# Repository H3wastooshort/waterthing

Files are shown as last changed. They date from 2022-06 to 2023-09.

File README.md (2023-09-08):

# waterthing
Wierd Garden Watering system

# very bad build guide
contact me if anything goes wrong (it will)
i will try to help if you actually want to build this
## controller
1. 3d print the case parts for the controller or come up with your own
2. put the parts in position and hotglue and screw them down
3. connect the components according to the schematic. the schematic is not the definitive way to do it though but rather a reflection of the current state of my build.
   the LoRa and LED module are optional.
4. upload the sketch and check if everything powers up and works
5. go mad because you cant find *that one error*
## gateway
1. (optional) print case and attach ESP32 LoRa Board 
2. connect antenna
3. upload sketch
4. connect to config AP and input WiFi credentials

# all shit blow this is outdated, just ignore it i will fix it some day....

## pump concept
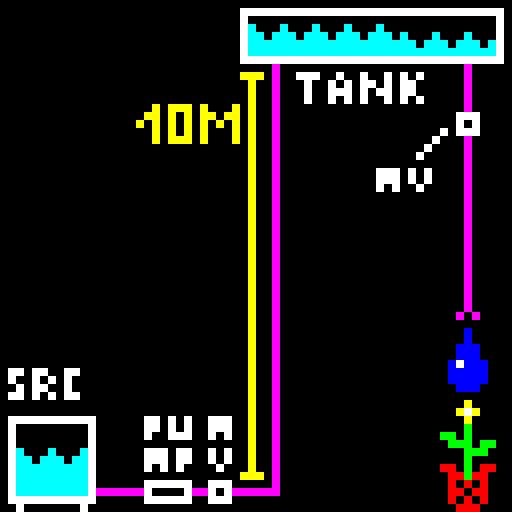
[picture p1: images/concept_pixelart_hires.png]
concept pixelart of the setup

 
The irrigation system is supposed to irrrigate via leaky hoses wich can only output little flow.

Most normal pumps can't efficiently provide this constant pressure, low flowrate flow, wich is bad becuase im planning to power this off of solar.

To fix this, the pump fills a tank about 10 meters higher, then shuts off and waits for the tank to drain out the leaky hoses after opening a magnet valve. Anadditional magnet valve is directly after the pump to prevent backflow.

This cycle is repeated until the desired amout of irrigation took place (or the water source is empty).

## tank concept
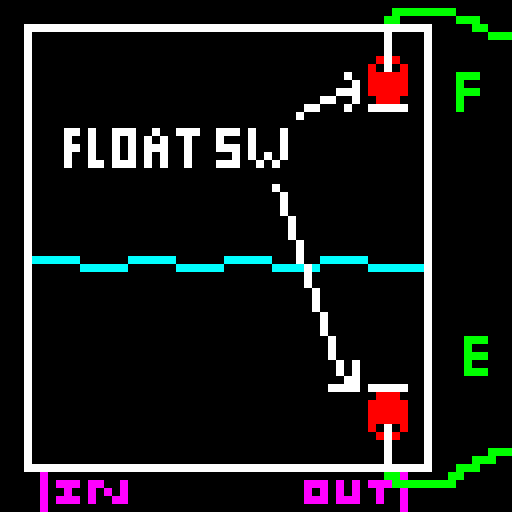
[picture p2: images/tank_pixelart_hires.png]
concept pixelart of the tank


The tank has a full and empty float switch. Both pull the arduino pin low when underwater

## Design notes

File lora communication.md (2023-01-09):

# General Scheme
[Magic Number][Packet ID][Packet Type][Data]

Magic Number is just 42

Packet ID increment individually on each side and rolls over to 0 when going over 255

## Gateway -> Water System
| Packet Type | Name | Anatomy | Description / Comment |
| --- | ---- | --- | --- |
| 0 | Current Time | [1 byte Packet ID of 230 time req] [UNIX Timestamp 32bit] | yes Y2K38, i'll just add the 60-something years when it rolls over to 1970 |
| 1 | Add Water to Irrigate | [1 byte Packet ID of challange] [Liters 2 bytes] [Auth Response 32 bytes] | |
| 2 | Cancel Irrigation | [1 byte Packet ID of challange] [Auth Response 32 bytes] | |
| 3 | Set Irrigation Timer | [1 byte Packet ID of challange] [Hour 1 byte] [Minute 1 byte] [Liters 2 bytes] [Auth Response 32 bytes] | |
| 241 | Reboot Notification | No Data | Packet sent once on boot |
| 250 | Ask for Auth challange | No Data | |
| 251 | Ping | | |
| 252 | Check Auth | [1 byte Packet ID of challange] [Auth Response 32 bytes] | Debug command to see if you have the right key without doing sth |
| 255 | ACK | [Packet ID] | |

## Water System -> Gateway
| Packet Type | Name | Anatomy | Description / Comment |
| --- | ---- | --- | --- |
| 0 | System Status | [4+4 bit status] [2 byte fixed point battery voltage]| Used to broadcast system state like STATUS_IDLE. Left 4 bits are system state, right 4 ones are more info (for ex in idle: alread watered, turned off, etc). fixed point battery voltage is a uint16_t divided by 100. max value would be 65.535V |
| 1 | Watering State | [4+4 bit status] [2 byte unsigned int: liters left] [2 byte unsigned int: liters called] | broadcasts watering state if currently watering |
| 230 | Request Time | No Data | |
| 240 | Reboot Notification | No Data | Packet sent once on boot |
| 249 | ACK | [1 byte packet ID] | |
| 250 | Auth challange | [1 byte Packet ID of 250 ask] [Auth challange 16 bytes] | |
| 251 | No Challange | [1 byte Packet ID] | Ask for a Challange Fist |
| 253 | Commands disabled | [1 byte Packet ID] | |
| 254 | Command Not Authenticated | [1 byte Packet ID] | |
| 255 | Command OK | [1 byte Packet ID] |

## Ground Sensor -> Water System
**JUST AN IDEA. PROBABLY WON'T HAPPEN**
| Packet Type | Name | Anatomy | Description / Comment |
| --- | ---- | --- | --- |
| 100 | Ground Data | [Sensor ID 1 byte] [Wetness 1 byte] | ground wetness is 0%-100% in 0.5% steps (so 0-200 in the wetness byte) |

## broadcast
 * Broadcast packets are removed from queue after they get acknowledged by the gateway or after 5 retransmits (spaced 5 seconds apart)
 * 

## system status
0bLLLLRRRR
### Left
| Bits | State |
| ---- | ----- |
| 0000 | Idle |
| 0001 | Pumping |
| 0010 | Emptying |
| 0011 | Afterdrain |
| 0100 | NO WATER |
| 0101 | LOW BATTERY |
| 0110 | NO TIME |
| 0111 | GENERAL FAIL |
### Right
#### Idle
| Bits | Extra |
| ---- | ----- |
| 0000 | Normal |
| 0001 | Off |
| 0010 | Done Today |
| 0011 | Rain |
#### General Fail
[] = 1 bit, each can be set individually

[Tank Sensors][RTC Missing][RTC Unset][Unused]

## (probably insecure) Authentication
 0. User saves 16 byte password from Water Systems Serial Console into the Gateway and requests an action.
 1. Gateway attempts up to 5 times to request an auth challange
 2. Water System respondes with a 16 byte random value as a challange.
 3. Gateway appends puts challange pass and packet data into sha-256 ([chal][pass][packet type][data] -> sha256)
 4. Gateway transmits the command id and parameters followed by the 32 bytes of the sha-256 hash
 5. arduino performs the same sha256 on challange value + security key and checks if they are identical
 6. command is accepted or rejected depending on hashes matching or not

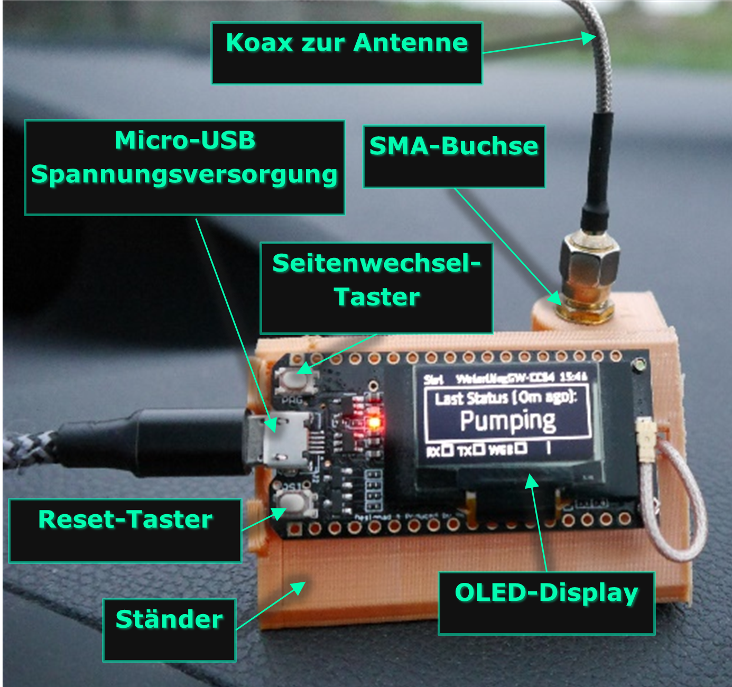
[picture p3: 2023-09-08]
images/gw overview.png

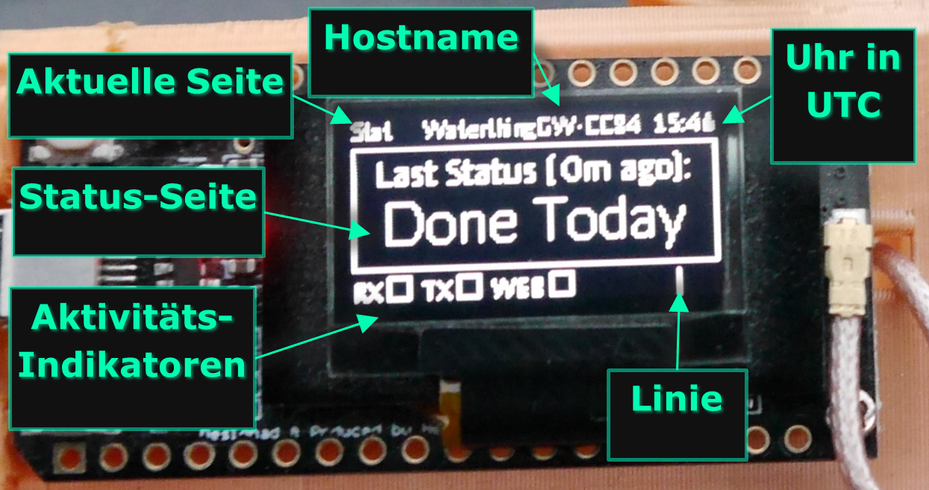
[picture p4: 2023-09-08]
images/gw ui.png

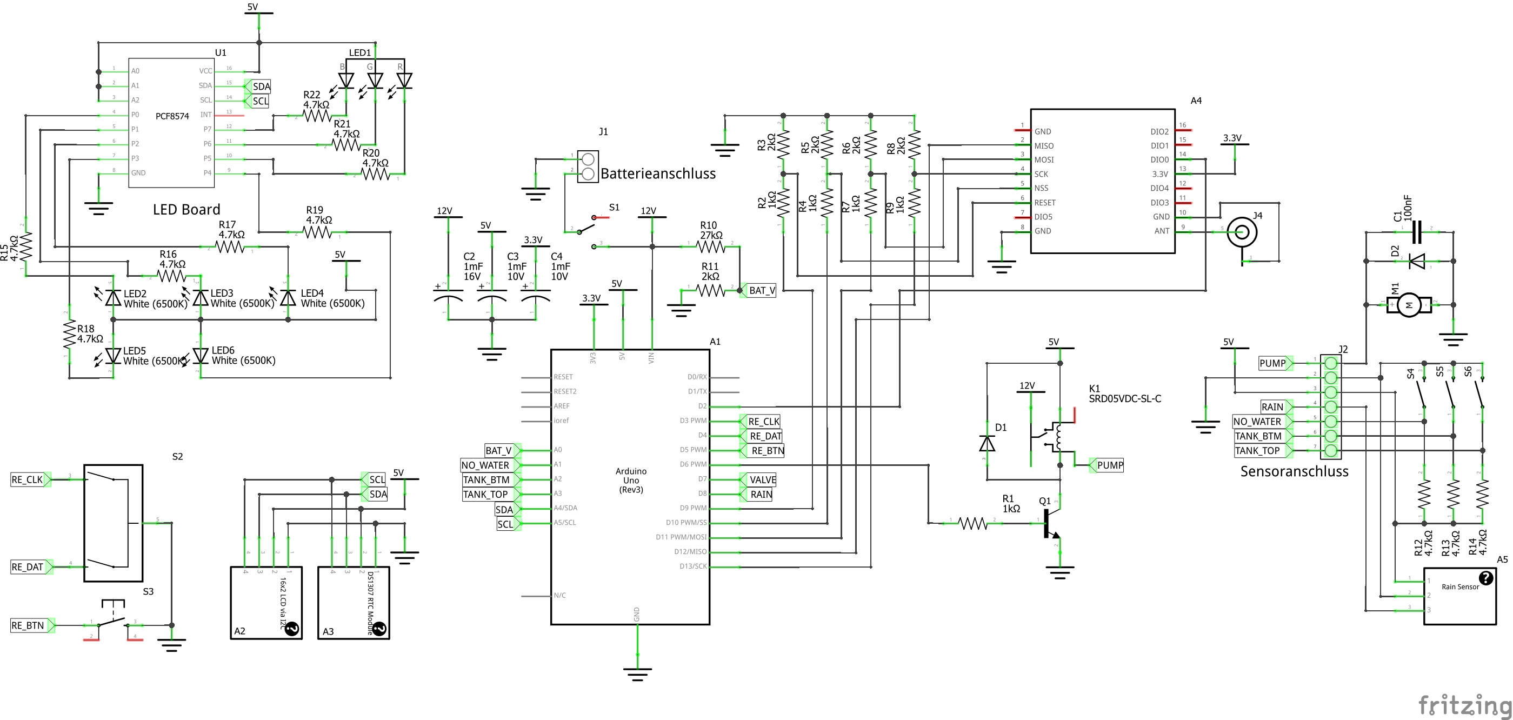
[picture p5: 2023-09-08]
images/wt circ_Schaltplan edit.png

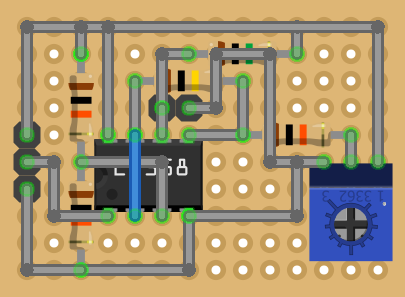
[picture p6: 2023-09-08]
images/opamp perfboarf_Steckplatine_sensitive.png

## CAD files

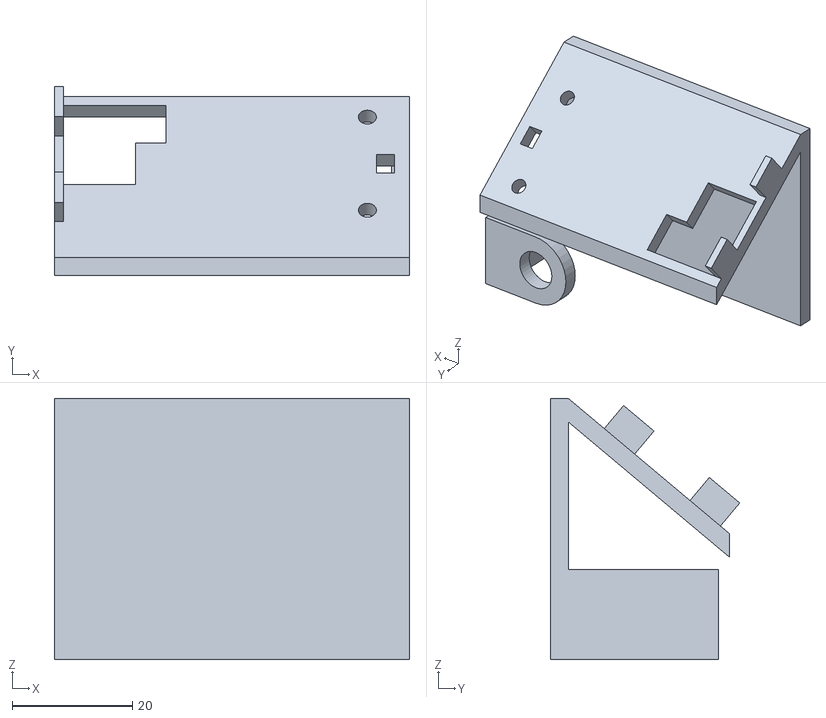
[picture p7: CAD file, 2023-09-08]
3d_models/GS Ständer.STL
59.0 x 31.5 x 43.4

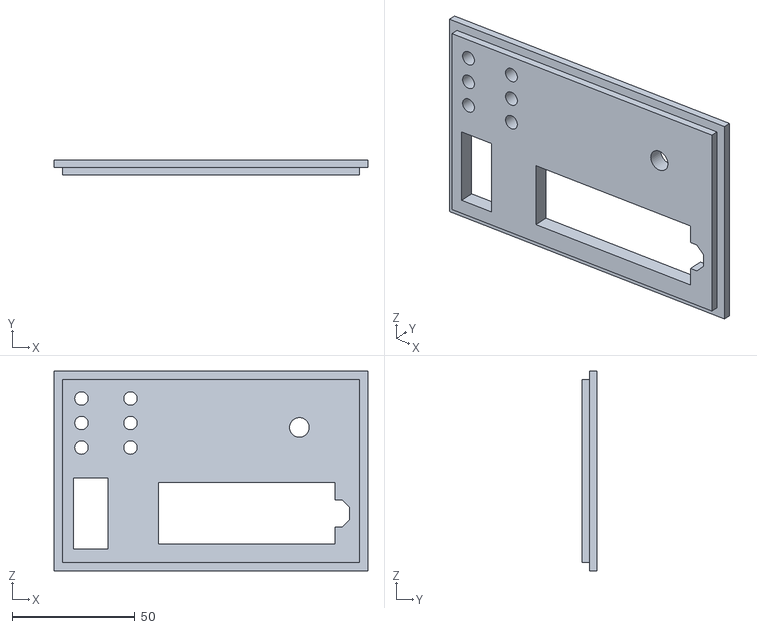
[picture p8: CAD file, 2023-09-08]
3d_models/deckel.STL
128.1 x 6.00 x 81.6

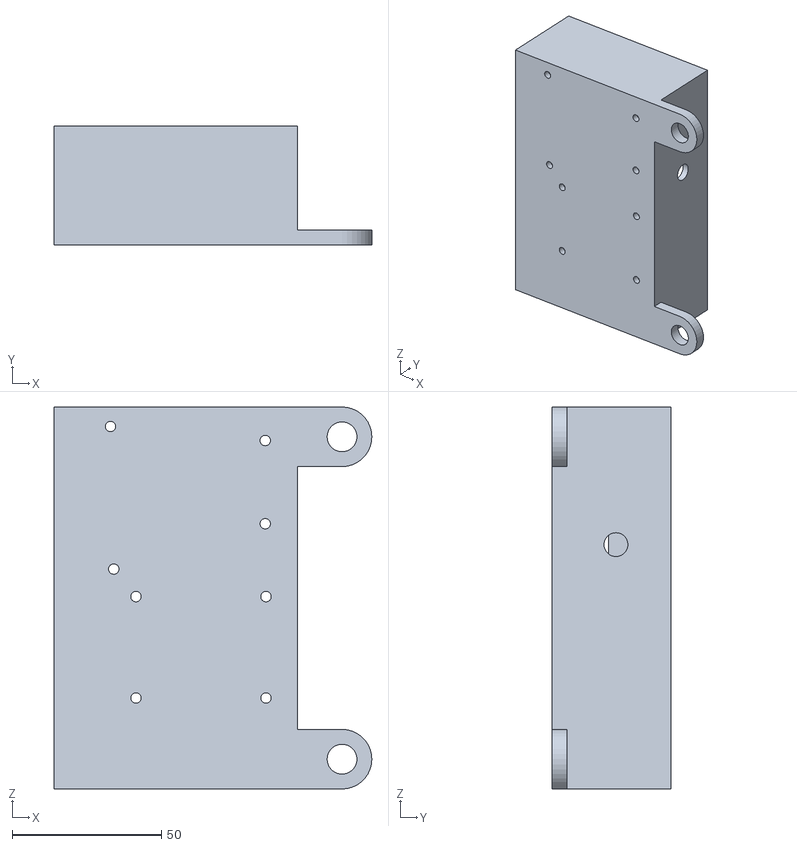
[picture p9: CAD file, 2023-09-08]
3d_models/gehäuse.STL
106.6 x 40.0 x 128.1

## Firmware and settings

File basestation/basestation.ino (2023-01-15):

//Gateway

#include <EEPROM.h>
#include <LoRa.h>
#include <Wire.h>
#include "fonts.h"
#include <OLEDDisplay.h>
#include <SSD1306Wire.h>  //https://github.com/ThingPulse/esp8266-oled-ssd1306
#include <WiFi.h>
#include <WiFiManager.h>  //https://github.com/tzapu/WiFiManager
#include <NTPClient.h>    //https://github.com/arduino-libraries/NTPClient
#include <RTClib.h>       //https://github.com/adafruit/RTClib/
#include <WebServer.h>
#include <EMailSender.h>  //https://github.com/xreef/EMailSender
#include <SPIFFS.h>
#define ARDUINOJSON_USE_LONG_LONG 1
#include <ArduinoJson.h>
#include <ESPmDNS.h>
#include <ArduinoOTA.h>
#include <map>
#include "mbedtls/md.h"

#undef LED_BUILTIN
#define LED_BUILTIN 25

#define RED_LED_PIN 12
#define GREEN_LED_PIN 13
#define BLUE_LED_PIN 21

#define LORA_FREQ 869525000        //869.525mhz is allowed to be used at 100mW 10% duty cycle (360 sec an hour) in germany (NO WARRANTY ON THAT!)
#define LORA_TX_PWR 20             // 20dbm/100mW is max
#define LORA_RETRANSMIT_TIME 5000  //time between retransmit attempts in ms
#define LORA_RETRANSMIT_TRIES 5
#define LORA_MAGIC 42
#define LORA_TX_INTERVAL 300000  //time between beacon broadcasts in ms
#define LORA_MAX_AIRTIME 340     //in seconds

#define LORA_CS_PIN 18
#define LORA_RST_PIN 14
#define LORA_DIO0_PIN 26

#define OLED_FPS 30
#define OLED_ADDRESS 0x3c
#define OLED_SDA_PIN 4
#define OLED_SCL_PIN 15
#define OLED_RST_PIN 16

#define EEPROM_SIZE 512

#define RTC_SDA_PIN 21
#define RTC_SCL_PIN 13

char host_name[18] = "WaterthingGW-XXXX";  // last 4 chars will be chip-id

SSD1306Wire oled(OLED_ADDRESS, -1, -1, GEOMETRY_128_64 /*, I2C_ONE, 200000*/);  //sometimes I2C_ONE is not decalred, sometimes it is, idk why
WiFiManager wm;
WiFiUDP ntpUDP;
NTPClient ntp(ntpUDP, "europe.pool.ntp.org", 0, 60000);
RTC_DS1307 rtc;
WebServer server(80);
EMailSender email("", "", "", "", 0);

//conf
struct settings_s {
  char conf_ssid[16] = "WaterthingGW";
  char conf_pass[16] = "CHANGE_ME_42";
  uint8_t lora_security_key[16] = { 0 };
  char alert_email[32] = "max.mustermann@example.com";
  char smtp_server[32] = { 0 };
  char smtp_user[32] = { 0 };
  char smtp_pass[32] = { 0 };
  uint16_t smtp_port = 465;  //usually 465 for SSL SMTP
  char web_user[32] = "waterthing";
  char web_pass[32] = "thisisnotsecure";
  uint8_t display_brightness = 255;
  char ntp_server[32] = "europe.pool.ntp.org";
  uint32_t crc;  //TODO: implement this
} settings;

//time
uint64_t current_timestamp;
bool rtc_ok = false;
uint8_t current_hour = 0;
uint8_t current_min = 0;

//lora
uint8_t lora_outgoing_packet_id = 1;      //increments every packet
byte lora_outgoing_queue[4][48] = { 0 };  //holds up to 4 messages that are to be sent with max 48 bits. first byte is magic, 2nd message id, 3nd is message type, rest is data. if all 0, no message in slot. set to 0 after up to 0 retransmits
uint8_t lora_outgoing_queue_idx = 0;      //idx where to write
uint64_t lora_outgoing_queue_last_tx = 0;
uint8_t lora_outgoing_queue_tx_attempts[4] = { 0 };
bool lora_tx_ready = true;
uint64_t lora_tx_start_millis = 0;
uint64_t lora_airtime = 0;  //in millis

byte lora_incoming_queue[4][48] = { 0 };      //holds up to 4 messages that are to be sent with max 48 bits.
uint8_t lora_incoming_queue_idx = 0;          //idx where to write
uint16_t lora_incoming_queue_len[4] = { 0 };  //lengths of recieved packages
byte lora_last_incoming_message_IDs[16] = { 0 };
uint8_t lora_last_incoming_message_IDs_idx = 0;

//shared stuff start
enum lora_packet_types_ws_to_gw {  //water system to gateway
  PACKET_TYPE_STATUS = 0,
  PACKET_TYPE_WATER = 1,
  PACKET_TYPE_TEST = 69,
  PACKET_TYPE_REBOOT = 240,
  PACKET_TYPE_WS_ACK = 249,
  PACKET_TYPE_AUTH_CHALLANGE = 250,
  PACKET_TYPE_NO_CHALLANGE = 251,
  PACKET_TYPE_CMD_DISABLED = 253,
  PACKET_TYPE_CMD_AUTH_FAIL = 254,
  PACKET_TYPE_CMD_OK = 255,
};

enum lora_packet_types_gw_to_ws {  //gateway to water system
  PACKET_TYPE_CURRENT_TIME = 0,
  PACKET_TYPE_ADD_WATER = 1,
  PACKET_TYPE_CANCEL_WATER = 2,
  PACKET_TYPE_SET_TIMER = 3,
  PACKET_TYPE_GW_REBOOT = 241,
  PACKET_TYPE_REQUST_CHALLANGE = 250,
  PACKET_TYPE_ACK = 255
};

//length is only packet data. add 3 for real packet size
uint8_t ws_to_gw_packet_type_to_length(uint8_t pt) {
  switch (pt) {
    case PACKET_TYPE_STATUS: return 3; break;
    case PACKET_TYPE_WATER: return 5; break;
    case PACKET_TYPE_TEST: return 5; break;
    case PACKET_TYPE_AUTH_CHALLANGE: return 17; break;
    case PACKET_TYPE_CMD_DISABLED: return 0; break;
    case PACKET_TYPE_CMD_AUTH_FAIL: return 1; break;
    case PACKET_TYPE_CMD_OK: return 1; break;
    case PACKET_TYPE_REBOOT: return 0; break;
    case PACKET_TYPE_WS_ACK: return 1; break;
    default: return 47; break;
  }
}

uint8_t gw_to_ws_packet_type_to_length(uint8_t pt) {
  switch (pt) {
    case PACKET_TYPE_ACK: return 1; break;
    case PACKET_TYPE_REQUST_CHALLANGE: return 0; break;
    case PACKET_TYPE_CURRENT_TIME: return 0; break;
    case PACKET_TYPE_ADD_WATER: return 35; break;
    case PACKET_TYPE_CANCEL_WATER: return 33; break;
    case PACKET_TYPE_SET_TIMER: return 37; break;
    case PACKET_TYPE_GW_REBOOT: return 0; break;
  }
}
//shared stuff end

//recieved stuff
int16_t last_lora_rssi = 0xFFFF;
int16_t last_lora_snr = 0xFFFF;
int32_t last_lora_freq_error = 0xFFFFFFFF;
uint64_t last_recieved_packet_time = 0;  //time in unix timestamp

byte last_wt_status = 0xFF;  //left bytes main status, right 4 bytes extra status
uint64_t last_wt_status_timestamp = 0;
uint16_t last_liters_left = 0xFFFF;    //0xFFFF means not known, 0x0000 means done
uint16_t last_liters_called = 0xFFFF;  //0xFFFF means not known, 0x0000 means done
uint64_t last_wt_liters_timestamp = 0;
float last_wt_battery_voltage = -1;
uint64_t last_wt_battery_voltage_timestamp = 0;
uint64_t last_wt_reboot_timestamp = 0;

//authed lora cmds
enum auth_state_e {
  AUTH_STEP_IDLE = 0,  //wait for entry in lora_auth_cmd_queue
  AUTH_STEP_TX_CHALLANGE_REQUEST = 1,
  AUTH_STEP_WAIT_CHALLANGE = 2,
  AUTH_STEP_TX_ANSWER = 3,
  AUTH_STEP_WAIT_CMD_SUCCESS = 4,
} auth_state;
byte last_wt_challange[16] = { 0 };       //if all 0, not valid/non recieved
byte lora_auth_cmd_queue[4][16] = { 0 };  //the data part of all authed commands to be sent.
uint8_t lora_auth_cmd_queue_idx = 0;
uint8_t lora_auth_packet_processing = 255;  //255 means invalid
byte last_auth_cmd_response = 0;            //0 means invalid
byte last_auth_challange_packet_id = 0xFF;
uint64_t last_auth_packet_millis = 0;

//web
char web_login_cookies[256][32];
uint8_t web_login_cookies_idx = 0;

std::map<byte, String> status_to_text{
  // SSSSEEEE
  { 0b11111111, "Unknown" },
  { 0b00000000, "Idle" },
  { 0b00000001, "Off" },
  { 0b00000010, "Done Today" },
  { 0b00000011, "Too Rainy" },
  { 0b00010000, "Pumping" },
  { 0b00100000, "Emptying" },
  { 0b00110000, "Afterdrain" },
  { 0b01000000, "NO WATER" },
  { 0b01010000, "LOW BAT." },
  { 0b01100000, "NO TIME" },
  { 0b01110000, "GEN. FAIL" },
  { 0b01110001, "PUMP FAIL" },
  { 0b01111000, "TS FAIL" },
  { 0b01110110, "RTC FAIL" },
  { 0b01110100, "RTC FAIL" },
  { 0b01110010, "RTC UNSET" },
  { 0b01111100, "TS+RTC FAIL" },
  { 0b01111110, "TS+RTC FAIL" },
  { 0b01111010, "TS+RTC FAIL" },
  { 0b01111101, "TOTAL FAIL" },
  { 0b01111111, "TOTAL FAIL" },
  { 0b01111011, "TOTAL FAIL" }
};

//display
enum gw_page_e { PAGE_STATUS = 0,
                 PAGE_WT = 1,
                 PAGE_LORA = 2,
                 PAGE_WIFI = 3 };
uint8_t disp_page = 0;
std::map<uint8_t, String> gw_page_to_text{
  { PAGE_STATUS, "Stat" },
  { PAGE_WT, "WT" },
  { PAGE_LORA, "LoRa" },
  { PAGE_WIFI, "WiFi" }
};
uint8_t rx_indicator_blink = 0;
//uint8_t tx_indicator_blink = 0;
uint8_t web_indicator_blink = 0;
uint8_t tx_indicator_pos = 0;

uint64_t last_disp_button_down = 0;
void IRAM_ATTR disp_button_down() {
  if (millis() - last_disp_button_down > 250) disp_page++;
  if (disp_page > 3) disp_page = 0;
  last_disp_button_down = millis();
}

//stuff
void update_time() {
  ntp.update();
  if (rtc_ok and rtc.isrunning() and !ntp.isTimeSet()) {  //if RTC is OK but the NTP server is not
    DateTime tnow = rtc.now();
    current_timestamp = tnow.unixtime();
    current_min = tnow.minute();
    current_hour = tnow.hour();
  } else {  //ELSE if ntp ok OR if rtc and ntp bad (ntp client will still calculate time with millis)
    current_timestamp = ntp.getEpochTime();
    current_min = ntp.getMinutes();
    current_hour = ntp.getHours();
  }
}

char randomASCII() {  //give random lowercase ascii
  switch (random(0, 3)) {
    default:
    case 0:
      return max(min(uint8_t(random(0, 24) + 'a'), uint8_t('z')), uint8_t('a'));
      break;

    case 1:
      return max(min(uint8_t(random(0, 24) + 'A'), uint8_t('Z')), uint8_t('A'));
      break;

    case 2:
      return max(min(uint8_t(random(0, 10) + '0'), uint8_t('9')), uint8_t('0'));
      break;
  }
}

void handle_lora_packet(int packet_size) {                                                 //TODO: maybe move magic checking here
  if (packet_size <= 48) {                                                                 //3840 is an erronious recieve
    for (uint8_t b = 0; b < 48; b++) lora_incoming_queue[lora_incoming_queue_idx][b] = 0;  //firstly clear

    for (uint8_t b = 0; (b < min(packet_size, 48)) and LoRa.available(); b++) {
      lora_incoming_queue[lora_incoming_queue_idx][b] = LoRa.read();
    }

    last_lora_rssi = LoRa.packetRssi();
    last_lora_snr = LoRa.packetSnr();
    last_lora_freq_error = LoRa.packetFrequencyError();
    lora_incoming_queue_len[lora_incoming_queue_idx] = min(packet_size, 48);
    lora_incoming_queue_idx++;
    if (lora_incoming_queue_idx >= 4) lora_incoming_queue_idx = 0;
  }
  LoRa.flush();  //clear packet if for some reason the is anything left
}

void handle_lora_tx_done() {
  LoRa.receive();
  lora_airtime += millis() - lora_tx_start_millis;  //add tx time
  lora_tx_ready = true;
}

//display
uint8_t alive_line_pos = 125;
bool alive_line_dir = false;  //false towards left, true towards right
void draw_display_boilerplate() {
  oled.clear();
  oled.setColor(WHITE);
  oled.setFont(Lato_Thin_8);
  oled.drawRect(0, 11, 127, 42);  //content outline

  //page number
  oled.setTextAlignment(TEXT_ALIGN_LEFT);
  oled.drawString(0, 0, gw_page_to_text[disp_page]);

  //name
  oled.setTextAlignment(TEXT_ALIGN_CENTER);
  oled.drawString(63, 0, host_name);

  //time on the right
  oled.setTextAlignment(TEXT_ALIGN_RIGHT);
  char time_buf[5];
  sprintf(time_buf, "%02d:%02d", current_hour, current_min);
  oled.drawString(127, 0, (String)time_buf);

  //rx/tx indicators
  oled.setTextAlignment(TEXT_ALIGN_LEFT);
  uint8_t bottom_pos = 0;
  oled.drawString(bottom_pos, 55, "RX");
  bottom_pos += oled.getStringWidth("RX") + 2;
  if (rx_indicator_blink > 0) {
    oled.fillRect(bottom_pos, 55, 8, 8);
    rx_indicator_blink--;
  } else oled.drawRect(bottom_pos, 55, 8, 8);
  bottom_pos += 8 + 4;
  oled.drawString(bottom_pos, 55, "TX");
  bottom_pos += oled.getStringWidth("TX") + 2;
  tx_indicator_pos = bottom_pos;
  //if (tx_indicator_blink > 0) {
  if (!lora_tx_ready) {
    oled.fillRect(bottom_pos, 55, 8, 8);
    //tx_indicator_blink--;
  } else oled.drawRect(bottom_pos, 55, 8, 8);
  bottom_pos += 8 + 4;
  oled.drawString(bottom_pos, 55, "WEB");
  bottom_pos += oled.getStringWidth("WEB") + 2;
  if (web_indicator_blink > 0) {
    oled.fillRect(bottom_pos, 55, 8, 8);
    web_indicator_blink--;
  } else oled.drawRect(bottom_pos, 55, 8, 8);
  bottom_pos += 8 + 4;

  //moving line to show its alive
  alive_line_pos += alive_line_dir ? 1 : -1;
  if (alive_line_pos >= 125) alive_line_dir = false;
  if (alive_line_pos <= bottom_pos) alive_line_dir = true;
  oled.drawLine(alive_line_pos, 55, alive_line_pos, 63);
}

void config_ap_callback(WiFiManager *myWiFiManager) {
  //put conf AP credentials on screen
  oled.clear();
  oled.setColor(WHITE);
  oled.setFont(Lato_Thin_8);
  oled.setTextAlignment(TEXT_ALIGN_LEFT);

  oled.drawString(0, 0, "Connect AP and visit");
  oled.drawString(0, 10, "http://192.168.4.1/");
  oled.drawString(0, 20, "SSID:");
  oled.drawString(0, 30, settings.conf_ssid);
  oled.drawString(0, 40, "Password:");
  oled.drawString(0, 50, settings.conf_pass);
  oled.display();
}

//web
void set_mail_conf() {
  email.setSMTPServer(settings.smtp_server);
  email.setNameFrom(host_name);
  email.setEMailFrom(settings.smtp_user);
  email.setEMailLogin(settings.smtp_user);
  email.setEMailPassword(settings.smtp_pass);
  email.setSMTPPort(settings.smtp_port);
  email.setIsSecure(false);

  email.setEHLOCommand(true);
  //email.setAdditionalResponseLineOnHELO(2);  //only use on versions without auto-add.resp.l.. works for german mailer GMX. you probably have to figure out your value by setting it higher, uncommenting EMAIL_SENDER_DEBUG in EMailSenderKey.h and reducing it when error says so
}

bool check_auth() {
  Serial.println(F("Authed Access Attempt"));
  bool authed = false;

  if (server.hasHeader("Cookie")) {
    String cookie_header = server.header("Cookie");
    uint16_t lc_start = cookie_header.indexOf("login_cookie=");
    uint16_t lc_end = cookie_header.substring(lc_start).indexOf("; ");
    if (lc_end == 0) lc_end = cookie_header.length() - lc_start;
    const char *login_cookie = cookie_header.substring(lc_start + 13, lc_end).c_str();

    //Serial.print(F(" * Header: "));
    //Serial.println(cookie_header);
    //Serial.print(F(" * Cookie: "));
    //Serial.println(login_cookie);
    //Serial.print(F(" * Cookie Length: "));
    //Serial.println(login_cookie.length());

    if (strlen(login_cookie) == 31) {
      for (uint16_t c = 0; c < 256; c++) {  //check if login cookie valid
        //Serial.print(F(" * Cookie Candidate: "));
        //Serial.println(correct_l_cookie);

        if (strcmp(login_cookie, (const char *)web_login_cookies[c]) == 0) {
          authed = true;
          break;
        }
      }
    }
  } else Serial.println(F(" * Cookie Header Missing"));

  Serial.print(F(" * "));
  Serial.println(authed ? F("SUCCESS") : F("FAIL"));
  Serial.println();
  return authed;
}

void rest_status() {
  web_indicator_blink += 1;
  DynamicJsonDocument stuff(1024);
  stuff["status"]["state"] = last_wt_status >> 4;
  stuff["status"]["extra"] = last_wt_status & 0b00001111;
  stuff["status"]["as_text"] = status_to_text[last_wt_status];
  stuff["status"]["timestamp"] = last_wt_status_timestamp;
  stuff["irrigation"]["left"] = last_liters_left;
  stuff["irrigation"]["called"] = last_liters_called;
  stuff["irrigation"]["timestamp"] = last_wt_liters_timestamp;
  stuff["battery"]["voltage"] = last_wt_battery_voltage;
  stuff["battery"]["timestamp"] = last_wt_battery_voltage_timestamp;
  stuff["other"]["last_reboot"] = last_wt_reboot_timestamp;
  stuff["lora_rx"]["last_rssi"] = last_lora_rssi;
  stuff["lora_rx"]["last_snr"] = last_lora_snr;
  stuff["lora_rx"]["last_freq_error"] = last_lora_freq_error;
  stuff["lora_rx"]["last_packet_time"] = last_recieved_packet_time;
  stuff["lora_tx"]["airtime"] = (double)lora_airtime / 1000;
  stuff["lora_tx"]["max_airtime"] = LORA_MAX_AIRTIME;
  stuff["gateway"]["wifi"]["ssid"] = WiFi.SSID();
  stuff["gateway"]["wifi"]["rssi"] = WiFi.RSSI();
  stuff["gateway"]["time"]["now"] = current_timestamp;
  stuff["gateway"]["time"]["rtc_ok"] = rtc_ok;
  stuff["gateway"]["time"]["ntp_ok"] = ntp.isTimeSet();
  char json_stuff[2048];
  serializeJsonPretty(stuff, json_stuff);
  server.sendHeader("Refresh", "10");
  server.send(200, "application/json", json_stuff);
}

void rest_login_get() {
  DynamicJsonDocument resp(128);
  server.send(200, "application/json", check_auth() ? "true" : "false");
}

void rest_login() {
  web_indicator_blink += 1;
  if (check_auth()) {
    server.send(200, "application/json", "{\"success\":\"Already Authenticated.\"}");
    Serial.println(F("Login Attempt: Already Authed"));
    return;
  }

  Serial.println(F("Login Attempt"));

  DynamicJsonDocument login(128);
  if (server.hasArg("plain")) deserializeJson(login, server.arg("plain"));
  String user = server.hasArg("plain") ? login["user"] : server.arg("user").c_str();
  String pass = server.hasArg("plain") ? login["pass"] : server.arg("pass").c_str();
  String correct_user = settings.web_user;
  String correct_pass = settings.web_pass;

  Serial.print(F(" * User: "));
  Serial.println(user);
  Serial.print(F(" * Pass: "));
  Serial.println(pass);
  Serial.print(F(" * Correct User: "));
  Serial.println(correct_user);
  Serial.print(F(" * Correct Pass: "));
  Serial.println(correct_pass);

  if (user.equals(correct_user) and pass.equals(correct_pass)) {
    for (uint8_t b = 0; b < 31; b++) web_login_cookies[web_login_cookies_idx][b] = randomASCII();
    web_login_cookies[web_login_cookies_idx][31] = 0;
    String cookiestring = "login_cookie=";
    cookiestring += web_login_cookies[web_login_cookies_idx];
    cookiestring += "; Path=/admin/; SameSite=Strict; Max-Age=86400";  //cookie kept for a day

    server.sendHeader("Set-Cookie", cookiestring);
    if (!server.hasArg("plain")) server.sendHeader("Refresh", "3;url=/admin/control.html");
    server.send(200, "application/json", "{\"success\":\"Authenticated\",\"login_cookie\":\"" + cookiestring + "\"}");
    Serial.println(F(" * SUCCESS"));
  } else {
    if (!server.hasArg("plain")) server.sendHeader("Refresh", "5;url=/admin/login.html");
    server.send(403, "application/json", "{\"error\":\"Credentials invalid.\"}");
    Serial.println(F(" * FAIL"));
  }

  Serial.println();
}

void rest_control() {
  web_indicator_blink += 1;
  if (!check_auth()) {
    server.send(403, "application/json", "{\"error\":403}");
    return;
  }
  uint16_t status_code = 200;
  DynamicJsonDocument resp(512);

  DynamicJsonDocument req(256);
  if (server.hasArg("plain")) deserializeJson(req, server.arg("plain"));

  if (req["call_for_water"].is<uint16_t>() or server.hasArg("call_for_water")) {
    for (uint8_t b = 0; b < 16; b++) lora_auth_cmd_queue[lora_auth_cmd_queue_idx][b] = 0;
    union {
      uint16_t water_call = 0;
      byte water_call_b[2];
    };
    water_call = server.hasArg("plain") ? req["call_for_water"] : server.arg("call_for_water").toInt();

    lora_auth_cmd_queue[lora_auth_cmd_queue_idx][0] = PACKET_TYPE_ADD_WATER;
    lora_auth_cmd_queue[lora_auth_cmd_queue_idx][1] = water_call_b[0];
    lora_auth_cmd_queue[lora_auth_cmd_queue_idx][2] = water_call_b[1];

    lora_auth_cmd_queue_idx++;
    if (lora_auth_cmd_queue_idx >= 4) lora_auth_cmd_queue_idx = 0;

    resp["success"] = "queued <water call> command";
  }

  else if (req["cancel_water"] or server.hasArg("cancel_water")) {
    for (uint8_t b = 0; b < 16; b++) lora_auth_cmd_queue[lora_auth_cmd_queue_idx][b] = 0;

    lora_auth_cmd_queue[lora_auth_cmd_queue_idx][0] = PACKET_TYPE_CANCEL_WATER;

    lora_auth_cmd_queue_idx++;
    if (lora_auth_cmd_queue_idx >= 4) lora_auth_cmd_queue_idx = 0;

    resp["success"] = "queued <cancel> command";
  }

  else if (req["set_timer"] or server.hasArg("set_timer")) {
    for (uint8_t b = 0; b < 16; b++) lora_auth_cmd_queue[lora_auth_cmd_queue_idx][b] = 0;
    union {
      uint16_t liters = 0;
      byte liters_b[2];
    };
    liters = server.hasArg("plain") ? req["set_timer"]["liters"] : server.arg("set_timer_liters").toInt();

    lora_auth_cmd_queue[lora_auth_cmd_queue_idx][0] = PACKET_TYPE_SET_TIMER;
    lora_auth_cmd_queue[lora_auth_cmd_queue_idx][1] = server.hasArg("plain") ? req["set_timer"]["hour"] : server.arg("set_timer_hour").toInt();
    lora_auth_cmd_queue[lora_auth_cmd_queue_idx][2] = server.hasArg("plain") ? req["set_timer"]["minute"] : server.arg("set_timer_minute").toInt();
    lora_auth_cmd_queue[lora_auth_cmd_queue_idx][3] = liters_b[0];
    lora_auth_cmd_queue[lora_auth_cmd_queue_idx][4] = liters_b[1];

    lora_auth_cmd_queue_idx++;
    if (lora_auth_cmd_queue_idx >= 4) lora_auth_cmd_queue_idx = 0;

    resp["success"] = "queued <set timer> command";
  }

  else {
    server.send(400, "application/json", "{\"error\":\"no command\"");
    return;
  }

  if (!server.hasArg("plain")) server.sendHeader("Refresh", "3;url=/admin/control.html");
  char buf[512];
  serializeJson(resp, buf);
  server.send(status_code, "application/json", buf);
}

void rest_control_status() {
  web_indicator_blink += 1;
  uint16_t status_code = 200;
  DynamicJsonDocument resp(128);

  uint8_t left_q = 0;
  for (uint8_t p = 0; p < 4; p++) {
    bool is_empty = true;
    for (uint8_t b = 0; b < 16; b++)
      if (lora_auth_cmd_queue[p][b] != 0) is_empty = false;
    if (!is_empty) left_q++;
  }

  resp["auth_state"] = auth_state;
  resp["left_in_queue"] = left_q;
  resp["last_auth_cmd_response"] = last_auth_cmd_response;
  resp["last_auth_packet_millis"] = last_auth_packet_millis;

  char buf[256];
  serializeJson(resp, buf);
  server.send(status_code, "application/json", buf);
}

void rest_admin_get() {
  web_indicator_blink += 1;
  if (!check_auth()) {
    server.send(403, "application/json", "{\"error\":403}");
    return;
  }
  uint16_t status_code = 200;
  DynamicJsonDocument resp(1024);
  //settings
  resp["wifi"]["conf_ssid"] = settings.conf_ssid;
  resp["wifi"]["conf_pass"] = settings.conf_pass;
  for (uint8_t b = 0; b < 16; b++) resp["lora"]["security_key"][b] = settings.lora_security_key[b];
  resp["mail"]["alert_email"] = settings.alert_email;
  resp["mail"]["smtp_server"] = settings.smtp_server;
  resp["mail"]["smtp_user"] = settings.smtp_user;
  //resp["mail"]["smtp_pass"] = settings.smtp_pass;
  resp["mail"]["smtp_port"] = settings.smtp_port;
  resp["web"]["user"] = settings.web_user;
  //resp["web"]["pass"] = settings.web_pass;

  char buf[2048];
  serializeJson(resp, buf);
  server.send(status_code, "application/json", buf);
}
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
void loop() {
  ArduinoOTA.handle();
  server.handleClient();
  update_time();

  update_display();
  handle_lora();

  delay(5);
}

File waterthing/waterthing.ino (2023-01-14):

//Bewässerungssystem

/*
  ====IMPORTANT====
  If you run into space issues (you will), install the Optiboot bootloader on your board (it saves about 1 kb space)
  and compile with the ATMega328P option in MiniCore (https://github.com/MCUdude/MiniCore)
  as that has the correct space limit and can turn on LTO (Link-time optimizations) to save even more space. good luck
*/

#include <EEPROM.h>
#include <LiquidCrystal_I2C.h>
#include "gfx.h"
#include <TimeLib.h>
#include <Wire.h>
#include <DS1307RTC.h>  //https://github.com/PaulStoffregen/DS1307RTC/
#include <math.h>
#include <pcf8574.h>  //https://github.com/MSZ98/pcf8574
#include <SPI.h>
#include <LoRa.h>  //https://github.com/sandeepmistry/arduino-LoRa
#include <avr/wdt.h>
#include "sha256_small.h"  //https://github.com/simonratner/Arduino-SHA-256

#define LOW_WATER_PIN A1
#define TANK_BOTTOM_PIN A2
#define TANK_TOP_PIN A3  //reused for water flow sensor when in direct mode. WARNING! change PCINT suff in setup() too!!
#define RAIN_DETECTOR_PIN 8
#define SENSOR_DEBOUNCE 1000
#define PUMP_PIN 6
#define VALVE_PIN 7
#define CONTROL_RELAY_INVERTED true

//pcf
#define LED_PCF_ADDR 0x3F
#define RED_LED_PIN 5
#define GREEN_LED_PIN 6
#define BLUE_LED_PIN 7
#define TB_SENSOR_LED 2  //tank bottom sensor indicator
#define TT_SENSOR_LED 1  //tank top sensor indicator
#define PUMP_LED 0
#define LORA_TX_LED 3
#define LORA_RX_LED 4

#define DEBOUNCE_DELAY 150
#define BTN_PIN 5          //PCINT
#define ENCODER_CLK_PIN 3  //WARNING! change PCINT suff in setup() too!!
#define ENCODER_DT_PIN 4
#define ENCODER_INVERT_DIRECTION false

#define LCD_BACKLIGHT_TIMEOUT 10000

#define BATTERY_VOLTAGE_PIN A0

#define EEPROM_MAGIC_NUMBER 42

#define LORA_FREQ 869525000        //869.525mhz is allowed to be used at 100mW 10% duty cycle (360 sec an hour) in germany
#define LORA_TX_PWR 20             //20dbm/100mW is max
#define LORA_RETRANSMIT_TIME 5000  //time between retransmit attempts in ms
#define LORA_RETRANSMIT_TRIES 5
#define LORA_MAGIC 42
#define LORA_TX_INTERVAL 1800000  //time between beacon broadcasts in ms (30min)
#define LORA_MAX_AIRTIME 340     //in seconds

//library stuff
LiquidCrystal_I2C lcd(0x27, 16, 2);
PCF8574 pcf(LED_PCF_ADDR);  //all addr pins to high

enum gfx_IDs {        //enum for naming display gfx ids
  GFX_ID_STATUS = 0,  //redefined dynamically
  GFX_ID_DYN_1 = 1,
  GFX_ID_DYN_2 = 2,
  GFX_ID_DYN_3 = 3,
  GFX_ID_UML_S = 4,
  GFX_ID_UML_A = 5,
  GFX_ID_UML_O = 6,
  GFX_ID_UML_U = 7,
  GFX_ID_ARROW_L = 126,
  GFX_ID_ARROW_R = 127
};

//structs are used to save to EEPROM more easily
struct settings_s {
  uint16_t tank_capacity = 10;                  //in L
  double battery_voltage_adc_divider = 68.267;  //1024 divided by this multiplier equals the battery voltage
  float battery_voltage_cutoff = 10.4;          //if this voltage is reached while the system is idle, a low battery waring is displayed. 0 means disable
  float battery_voltage_reset = 11.4;           //if this voltage is reached while the system is in low batters state, the system is set back to idle
  int16_t max_mins_per_refill = -1;             //error is thrown if the pump takes longer than that to fill the tank (5L/min pump wont take more than 5 minutes to fill a 20L tank)
  uint8_t afterdrain_time = 5;                  //keep draining for this amount of time after a cycle finishes to dry the tank out
  uint16_t clicks_per_liter = 1000;
  bool low_water_on_level = LOW;     //level of low water pin when the low water sensor detects low water. sensor will probably be mounted upside-down so no water means low
  bool tank_bottom_on_level = HIGH;  //level of TANK_BOTTOM_PIN when water has reached the bottom sensor. sensor will probably be mounted upside-down so on means high
  bool tank_top_on_level = LOW;      //level of TANK_TOP_PIN when water has reached the top sensor
  bool rain_detected_on_level = LOW;
  uint8_t rain_minutes_til_block = 5;    //if rain is detected for more than this time, it is officially raining
  uint16_t rain_minutes_til_clear = 60;  //if its not rainf or at least this time, watering will resume as normal
  bool block_water_after_rain = false;
  byte lora_security_key[16];
  uint8_t lora_enable = 0;   //0=off, 1=broadcast only, 2=control
  uint8_t pump_timeout = 0;  //in minutes. if filling the tank takes longer than this value, the system goes into a fail state
  //uint32_t crc; //maybe verify with a crc32 here
} settings;

struct i_timer_s {
  int8_t start_hour = 0;
  int8_t start_minute = 0;
  uint16_t fillings_to_irrigate = 0;  //how many tank fillings to irrigate. when 0, system is turned off.
  uint8_t last_watering_day = 0;
  uint16_t liters_to_pump = 0;  //when in direct mode (no tank) how much liters to pump out
} irrigation_timer;

//and also just to organize things
struct c_error_s {
  bool rtc_missing = false;
  bool rtc_unset = false;
  bool tank_sensors_irrational = false;
  bool lora_missing = false;
  bool pump_timed_out = false;
} component_errors;

//enums for easier code reading
enum system_state_e {
  STATUS_IDLE = 0,         //doing nothing
  STATUS_PUMPING = 1,      //pumping water in tank
  STATUS_EMPTYING = 2,     //emptying tank
  STATUS_AFTERDRAIN = 3,   //fully drain out tank
  STATUS_NO_WATER = 4,     //cant get water from tank
  STATUS_LOW_BATTERY = 5,  //low battery voltage
  STATUS_NO_TIME = 6,      //clock not set
  STATUS_GENERAL_FAIL = 7
};

//global system variables
enum system_state_e system_state = STATUS_IDLE;
tmElements_t current_time;
byte mcusr_copy;

struct sensor_s {
  bool low_water = false;
  bool tank_bottom = false;
  bool tank_top = false;
  bool rain_detected = false;
  uint32_t water_flow_clicks = 0;
  uint32_t rain_start_millis = 0xFFFFFFFF;
  uint32_t rain_end_millis = 0xFFFFFFFF;
  float battery_voltage = 0;
} sensor_values;

uint16_t tank_fillings_remaining = 0;  //if over 0, run pumping stuff til 0. is in tank fillings normally, in liters in direct mode
uint64_t cycle_finish_millis = 0xFFFFFFFF;
uint32_t pumping_start_millis = 0;  //0 if never started

//lora variables
// it would have been a better idea to have an outgoing and incoming array with structs in it instead of multiple for each attribute
uint8_t lora_outgoing_packet_id = 1;      //increments every packet
byte lora_outgoing_queue[4][48] = { 0 };  //holds up to 4 messages that are to be sent with max 48 bits. first byte is magic, 2nd message id, 3nd is message type, rest is data. if all 0, no message in slot. set to 0 after up to 0 retransmits
uint8_t lora_outgoing_queue_idx = 0;      //idx where to write
uint32_t lora_outgoing_queue_last_tx = 0;
uint8_t lora_outgoing_queue_tx_attempts[4] = { 0 };
bool lora_tx_ready = true;
uint32_t lora_tx_start_millis = 0;
uint32_t lora_airtime = 0;  //in millis
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

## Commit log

2022-06-14 clock menu done and other stuff fixed
    [waterthing.ino]
2022-06-14 button que system added so buttont dont have to exec in interrupts
    also wokwi diagram
2022-06-14 fixed bug with queueing
    [waterthing.ino]
2022-06-14 float switches now invertible
2022-06-14 tank error detection and better error screen
    [waterthing.ino]
2022-06-14 rotary encoder implemented
    thought that would be harder... (famous last words)
2022-06-14 better button handler
2022-06-16 a lot of things: battery voltage monitoring, better status graphics, other stuff
2022-06-16 battery menu almost done
2022-06-16 arduino cant do sprintf() float by default. note added
2022-06-19 using dtostrf instead of printf('%f') for floats
2022-07-10 starting to add a "direct mode"
    in direct mode, the pump is attached to the irrigation stuff directly instead of filling a gravity powered feed tank
2022-07-17 sensor config page
2022-07-21 more lora stuff and water detector circuit
2022-07-21 led and lora stuff
2022-07-27 making rain sensor timing based and more gw stuff
2022-07-30 gw fixed OLED issues and login stuff
    [basestation.ino]
2022-07-30 use standard functions instead of my nonsense and added reset button
2022-07-30 gw mail sending routine (still broken)
    [basestation.ino]
2022-07-31 ws led pcf activity LED
2022-07-31 gw rough auth state machine prototype
2022-08-01 testing on real hardware made me find some rather goofy bugs
    also the arduino ide had some strong opinions on formatting
    [waterthing.ino]
2022-08-05 add watchdog. try fixing stl issue
    [basestation.ino, waterthing.ino]
2022-08-05 fuck std::map on arduino. also fixed state updates not being sent
    [waterthing.ino]
2022-08-05 fix lora pycket length
    [basestation.ino, waterthing.ino]
2022-08-05 trying to debug lora crashes
    [basestation.ino, waterthing.ino]
2022-08-05 fix dumb ui bug
    [basestation.ino, waterthing.ino]
2022-08-06 fixed small things and mate adc divider configureable
    [basestation.ino, waterthing.ino]
2022-08-07 wt voltage divider cal, gw html, concept code for moisture sensors
2022-08-22 fixed really small and dumb bug that prevented gw dedup working, merged status and battery packet
    [basestation.ino, waterthing.ino]
2022-08-22 i still did not fix it fuck
    [basestation.ino]
2022-08-22 finally got another really dumb bug
    [basestation.ino, waterthing.ino]
2022-08-29 finally fixed the crashing. yay
    [basestation.ino, waterthing.ino]
2022-08-31 fixed login bug, added login bug
    [basestation.ino, waterthing.ino]
2022-09-01 i finally found out why lora stops working on wt
    good news i found the issue, bad news its memory corruption!
    the component_errors.lora_missing flag gets randomly turned to true after 30 or so second. for fucks sake, how do i even start to debug this without being able to attach a debugger?!?!
    [basestation.ino]
2022-09-01 fixed the memory corruption. hell yes
    [waterthing.ino]
2022-09-01 ok now i fixed the memory corruption
    [waterthing.ino]
2022-09-04 new reboot packet type, fix bug
    note: put packet finish stuff in function
    did this yesterday
    [basestation.ino, waterthing.ino]
2022-09-05 fixed my dumbass not understanding the << operator and mixing up min() and max()
    [basestation.ino, waterthing.ino]
2022-09-05 finally fixed immideate tx after state change
    [waterthing.ino]
2022-09-06 dumb fixes and stuff
    [basestation.ino, waterthing.ino]
2022-09-06 fix very dumb bugs i just made
    [basestation.ino, waterthing.ino]
2022-09-06 im not quite sure what im doing right now im still feeling tired
2022-09-06 i give up, reverting to f175f6487c9246ed514564a71b8e4018e2f05f57
    [basestation.ino, waterthing.ino]
2022-09-07 gateway reboot packet added
    [basestation.ino, waterthing.ino]
2022-09-07 its not working again, maybe this helps? also fixed possible memory corruption on gw
    [basestation.ino, waterthing.ino]
2022-09-07 fuuuuck its doing the same shit again as yesterday whyyy. hope this fixes it
    [basestation.ino]
2022-09-07 i dont want to deal with this shit right now, reverting to 665ccd5d976b6fe03dbfdd78975ce8bb946583d4
    [basestation.ino, waterthing.ino]
2022-09-07 Revert "i dont want to deal with this shit right now, reverting to 665ccd5d976b6fe03dbfdd78975ce8bb946583d4"
    This reverts commit 936a398a90a355948a7d049ee160ecfc1b0717c2.
    [basestation.ino, waterthing.ino]
2022-09-07 i think it works. read full message
    when sending 2 packets back-to-back it can happen that both sides tx at the same time. i will have to fix that
    [basestation.ino, waterthing.ino]
2022-09-08 more sensible done state after setting timer
2022-09-08 debounce float switches
2022-09-08 whoops wrong compare op
    [waterthing.ino]
2022-09-10 reducing bandwidth to 125khz. see desc
    frequency error (at least on my devices) is often about 8khz between devices, which means that with a 250khz bandwidth, i could easily tx a few khz outside the freqency band of 869.4Mhz-869.65Mhz on which up to 500mW ERP at 10% duty cycle is allowed. this would realistically not be an issue but this is supposed to be published and i dont want to piss off the Bundesnetzagentur (or anyone else on the band)
    [basestation.ino, waterthing.ino]
2022-10-04 how do i force avr assembly into a c++ file? help
2022-10-14 why is the gw crashing now?
    [basestation.ino]
2022-10-14 what? why does that crash stuff?
    [basestation.ino]
2022-10-18 small stuff, switch to better random
2022-10-18 switching to optiboot+mightycore for space savings
2022-10-20 the debug rest stopped crashing. i dont know why
    [basestation.ino]
2022-10-20 phew. that fixed it
    [basestation.ino]
2022-10-22 encountering a wierd issue
    18:08:38.929 -> Incoming LoRa Packet:
    18:08:38.929 -> * Length: 19
    18:08:38.929 -> * Content: 2A 06 FA 05 [...]
    18:08:38.929 -> Magic Correct.
    18:08:38.929 -> Packet type: Challange
    18:08:38.929 -> * Cleared Packet ID: 0
    it clears by the packed id contained in byte 3 (starting from byte 0)
    for some reason though it clears pkt. id 0 not 5
    [basestation.ino, waterthing.ino]
2022-10-24 better rain detection circuit
2022-10-27 oh god i think its memory corruption from SOMEWHERE again
    commenting out everything but the for-loop and print statement on the hexs func rsults in the check_auth() func being called after every cycle of the for loop after hasArg("submit_lora") (line 570)
2022-10-28 small changes to simple water sensor
2022-10-28 HOW?! How did that fix this?!
    [basestation.ino]
2022-10-28 BIG improvement on responding
    hopefully this prevents both TXing at the same time
    [basestation.ino, waterthing.ino]
2022-10-28 finally fixed that fucking hex string conversion func
    [basestation.ino]
2022-10-28 un-added bug that could cause mem corruption
    [basestation.ino]
2022-10-29 worked on rain detection
    also barely fit more debug some more debug stuff into flash
    also a slightly different led animation
2022-11-05 gm small fix
    also disp shows airtime on GW
    [basestation.ino]
2022-11-05 fixed dumb suff
    forgot to set tx_start_millis on wt
    incorrect casting in at% calculation
    now we're mathing with big boy numbers
    [basestation.ino, waterthing.ino]
2022-11-05 more stupid stuff
    size issues on wt again
    integer overflows due to some 1000s not being longs (god i hate that shit)
    forgot a pair of () on gw
    [basestation.ino, waterthing.ino]
2023-01-01 new arduino auto-format
2023-01-02 add bugs, working on MITM attack fix
    [basestation.ino, waterthing.ino]
2023-01-02 changed led colors
2023-01-04 added set timer packet
2023-01-04 fixed funny bugs
    set timer packet length was set 1 byte to short
    [basestation.ino, waterthing.ino]
2023-01-07 fixed lora comms document
    [waterthing.ino]
2023-01-09 added pump timeout
2023-01-11 fixed rain logic (again)
    ignore the mess that arose from cutting out even more stuff
    [waterthing.ino]
2023-01-11 fixed rain logic ( again again )
    [waterthing.ino]
2023-01-15 fixed issue with mail
    i mixed up && with a == somehow
    [basestation.ino]
2023-01-27 more sensitive versions of the rainwater detectors
    i severely underestimated the resistance of rain water
2023-09-08 3d models
    [GS Ständer.STL, deckel.STL, gehäuse.STL]
